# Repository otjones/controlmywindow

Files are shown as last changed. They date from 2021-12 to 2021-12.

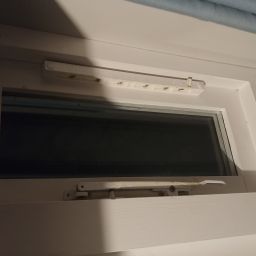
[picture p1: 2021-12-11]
client/images/webclip.jpg

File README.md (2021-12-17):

# controlmywindow
A project to control my living room window and collect and analyse air quality and weather data

Source code split into:
-----------------------
Server - code to run on the Raspberry Pi  
Client - code hosted to run the dashboard on controlmywindow.co.uk  
Analysis - scripts to  estimate database size and perform data analysis  

3D STL files for actuator assembly included   

Recorded data from 12.05 20:27:09 to 12.16 01:40:20 (BST)
---------------------------------------------------------
log.json in repo

Demonstration video:
--------------------
https://youtu.be/NgbbmP9EjUA

Description of all source files
===============================

/server/src/ST7735  - libraries for LCD display  
/server/src/bme280  - libraries for air quality sensor  
/server/src/fonts...  - font files for LCD display  
/server/src/i2cdevice  - I2C libraries for communication with Enviroboard from Raspberr Pi  
/server/src/app.js  - main Node.js file for hosting the server and handling requests  
/server/src/endStop.py  - watches microswitches and stoppes the motor when triggered. Is spawned by app.js and runs continuously  
/server/src/messageServer.py  - hosts a localhost webserver to control the LCD display. Accepts /message/<body> requests from app.js  
/server/src/motorBACKWARD.py  - sets motor to turn in one direction indefinitely (until stopped by another command)  
/server/src/motorFORWARD.py  - same as above in reverse direction  
/server/src/motorSTOP.py  - stops the motor  
/server/src/weather.py  - reads the sensor data from the Pimoroni Enviro board and prints the result, spawned and read by worker.js  
/server/src/worker.js  - file of Javascript functions written to carry out repeatable tasks, called from app.js  
  
/client/css/  - CSS files generated by Webflow  
/client/images/  - favicon and webclip image files  
/client/js/  - Javascript files generated by Webflow (for UI interactions such as hover effects on buttons)  
/client/index.html  - main page for the dashboard, mix of Webflow generated HTML and custom HTML, including custom form for sending messages to LCD screen  
/client/script.js  - Custom Javascript file with functions for plotting all graphs, sending motor control requests (onCLick) and getting the window status (on page load)  
  
/analysis/insights.py  - script for running a CLI in a terminal to interactively plot data, plot the derivative of the data, print out temperature drop events, humidity spike events, and a routine for testing any two datasets for the sample Pearson's correlation coefficient  
/analysis/jsonSize.py  - the script used for estimating the database size  
  
/gear.STL  - Gear used in assembly  
/pinion.STL  - Pinion used in assembly. A right angled bracket was also stuck to the side of the pinion to actuate end stop switch  
/window.STL  - Main window mount clips over window frame and locks into place over the protrusion (shown in video)  
  
Parts list
==========
  
Motor - FIT0489-D DC GEARED MOTOR, BRUSHED (Farnell)  
Motor driver - SparkFun Motor Driver - Dual TB6612FNG (1A)  
Microswitches x2 - M140T01-AE0507A MICROSWITCH, SPDT, 5A, LONG LEVER (Farnell)  
Raspberry Pi 4 Model B  
Pimoroni Enviro Board - PIM486 ENVIRO PHAT BOARD, ENVIRO, AIR QUALITY (Farnell)  
Power supply (15v 1.5A) with step down to 12v and split to motor voltage of motor driver and another step down to 5v USB 3A  
  
ngrok for Linux

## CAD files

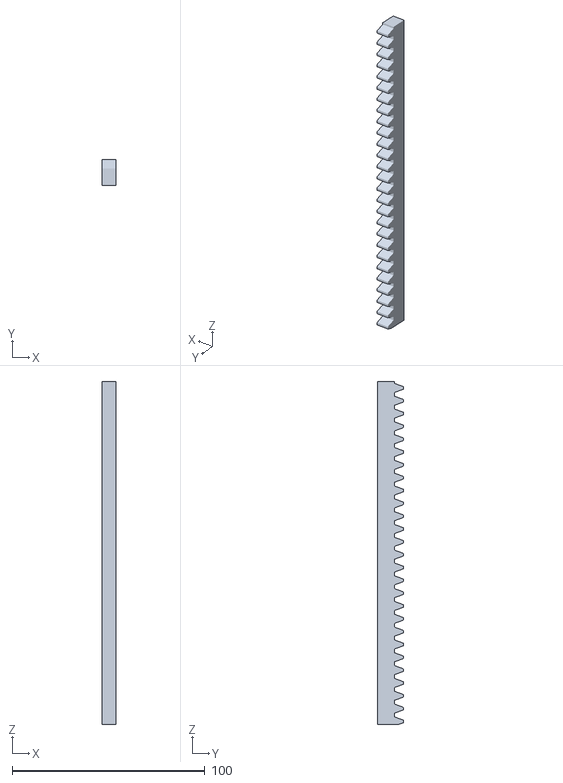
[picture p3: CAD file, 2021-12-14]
pinion.STL
7.01 x 13.5 x 177.8

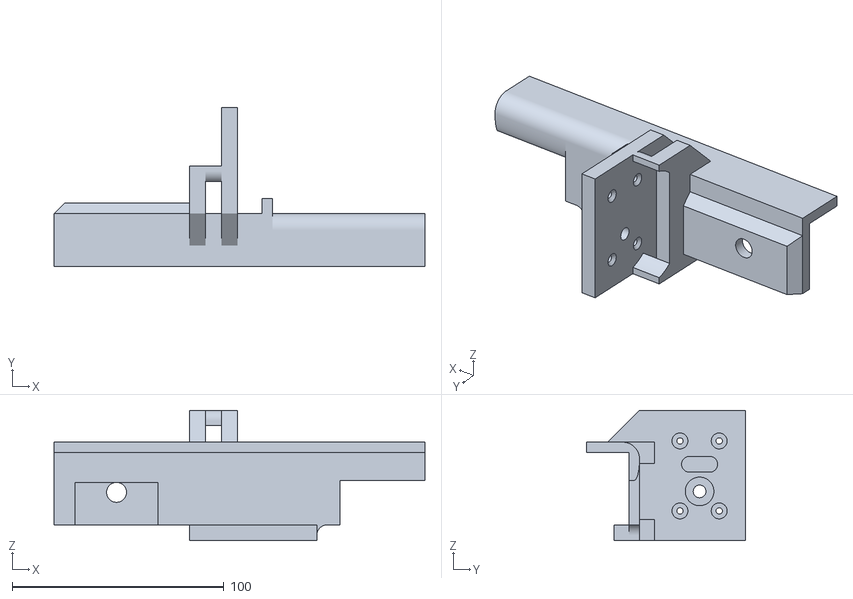
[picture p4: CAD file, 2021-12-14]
window.STL
175.0 x 75.0 x 61.5

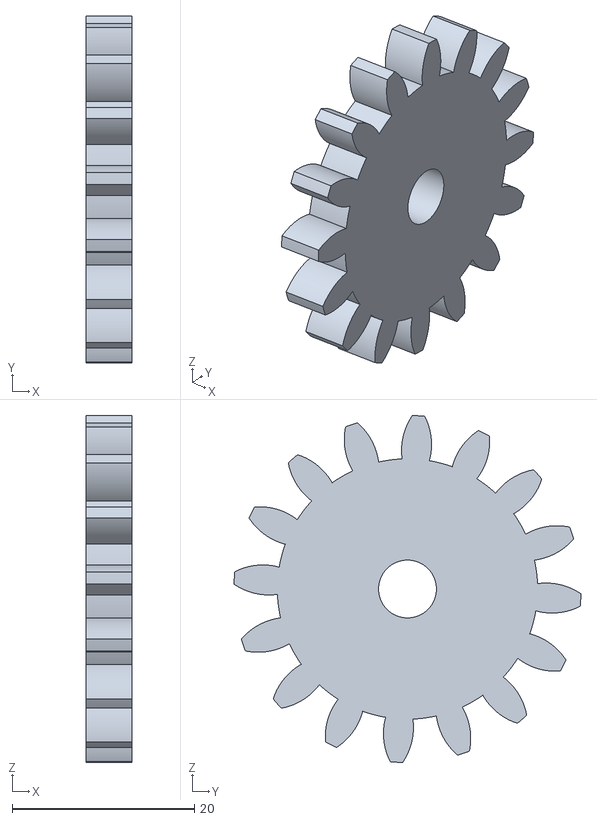
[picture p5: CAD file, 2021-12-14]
gear.STL
5.08 x 38.1 x 38.1

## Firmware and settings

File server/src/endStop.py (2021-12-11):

import RPi.GPIO as GPIO
import time

motorPin = 5
motor1 = 6
motor2 = 13
endPin1 = 4
endPin2 = 16
GPIO.setmode(GPIO.BCM)

GPIO.setwarnings(False)
GPIO.setup(motorPin,GPIO.OUT)
GPIO.setup(motor1,GPIO.OUT)
GPIO.setup(motor2,GPIO.OUT)
GPIO.setup(endPin1,GPIO.IN, pull_up_down=GPIO.PUD_UP)
GPIO.setup(endPin2,GPIO.IN, pull_up_down=GPIO.PUD_UP)

end = False

def motorStop(end):
    GPIO.output(motor1, 0)
    GPIO.output(motor2, 0)
    GPIO.output(motorPin, 0)
    end = True
    return end

while True:
    if not GPIO.input(endPin1) or not GPIO.input(endPin2):
        if end:
            pass
        else:
            end = motorStop(end)
    else:
        end = False
        pass
    time.sleep(0.01)

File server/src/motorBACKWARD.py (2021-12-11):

import RPi.GPIO as GPIO
import time

motorPin = 5
motor1 = 6
motor2 = 13
endPin = 16
GPIO.setmode(GPIO.BCM)
GPIO.setup(endPin,GPIO.IN, pull_up_down=GPIO.PUD_UP)

if GPIO.input(endPin):

    GPIO.setwarnings(False)
    GPIO.setup(motorPin,GPIO.OUT)
    GPIO.setup(motor1,GPIO.OUT)
    GPIO.setup(motor2,GPIO.OUT)

    GPIO.output(motor1, 0)
    GPIO.output(motor2, 1)
    GPIO.output(motorPin, 1)
